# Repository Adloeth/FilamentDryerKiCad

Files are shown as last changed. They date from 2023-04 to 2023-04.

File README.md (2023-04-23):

# FilamentDryer KiCad

This is my first ever PCB design, nothing too interesting.

As this is my first electronic project with a custom PCB, this whole thing is a mess and I wouldn't do anything like this ever again ^^'

A lot of lessons were learned. I ordered and tested the board and everything is working as expected, but because I was ignorant there is a chance the whole PCB is a ticking bomb especially considering I totally forgot everything about it. Younger me might have miscalculated (or simply not calculated at all) some power usage somewhere, and it is possible a resistor, trace, component or whatever burst in flames and magic smokes.

## The Board

There aren't really that many components on this board, except a few resistors and MOSFETs. It mostly is a scaffolding for other PCBs : 
* Arduino Nano
* TCA9548A I²C multiplexer
* LM2596 buck converter to lower the voltage to 5V for the Arduino

The board has other peripherals :
* The DC 12V 5W 80°C PTC heating element
* AT24C256, an I²C EEPROM to store the temperature and humidity graphs.
* DHT22 sensor to control the heating element
* Two I²C OLED screens
* PC fan
* Loadcell and the HX711 (it's amplifier) to measure how many filament is left
* A few buttons to control everything

The Arduino code can be found on [another repository](https://github.com/Adloeth/FilamentDryer).

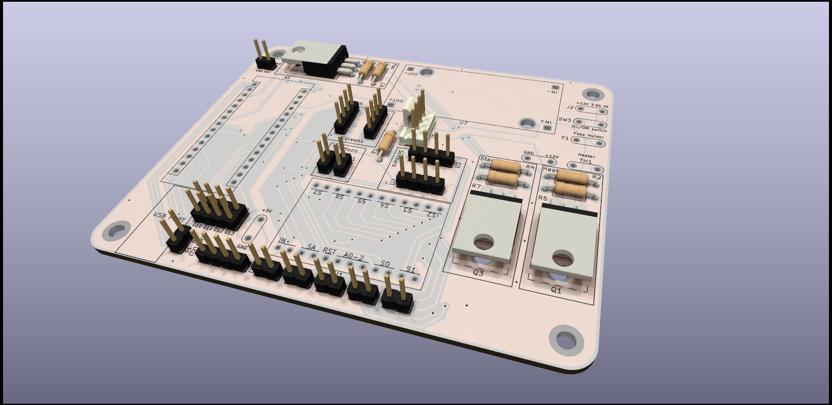
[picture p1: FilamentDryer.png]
Little rendering


## Why I did all this

My 3D printer had a moisture problem (Apparently PETG doesn't like humidity that much). The solution to this problem was to put the filament in the oven for a few hours, but I am not dumb enough to put a plastic that can have any number of toxic additives in the same oven I used to bake the food I eat.

Some companies sell filament dryers, the lowest of which was 60€ at the time. After looking around on the Internet I found a [series of videos](https://www.youtube.com/watch?v=IPKQCZ75Vwg&list=PLU5lZZLWyxXBlUrfcWFHtYylawElMm2N6) from [My Tech Fun](https://www.youtube.com/@MyTechFun) comparing several dryers, the ones at the lowest prices were surprisingly ineffective and required a lot of DIY to make them more efficient. While the most expansive were absolutely overkill.

So I decided to make everything myself, making sure my dryer was working where the other ones wouldn't and that some features only the priciest had were available to mine. The whole BOM was to be around 70€, which was good enough. It even had extruded polystyrene for thermal insulation !

Ultimately, putting my filament in an IKEA 10.6L 365+ with a layer of silica gel at the bottom solved the moisture issue and this project only served for me to learn how to make and order PCBs using KiCad and [JLCPCB](https://jlcpcb.com/), which is a very useful skill for my other future projects. Maybe one day I'll properly finish it, especially if I ever buy polyamide filaments.

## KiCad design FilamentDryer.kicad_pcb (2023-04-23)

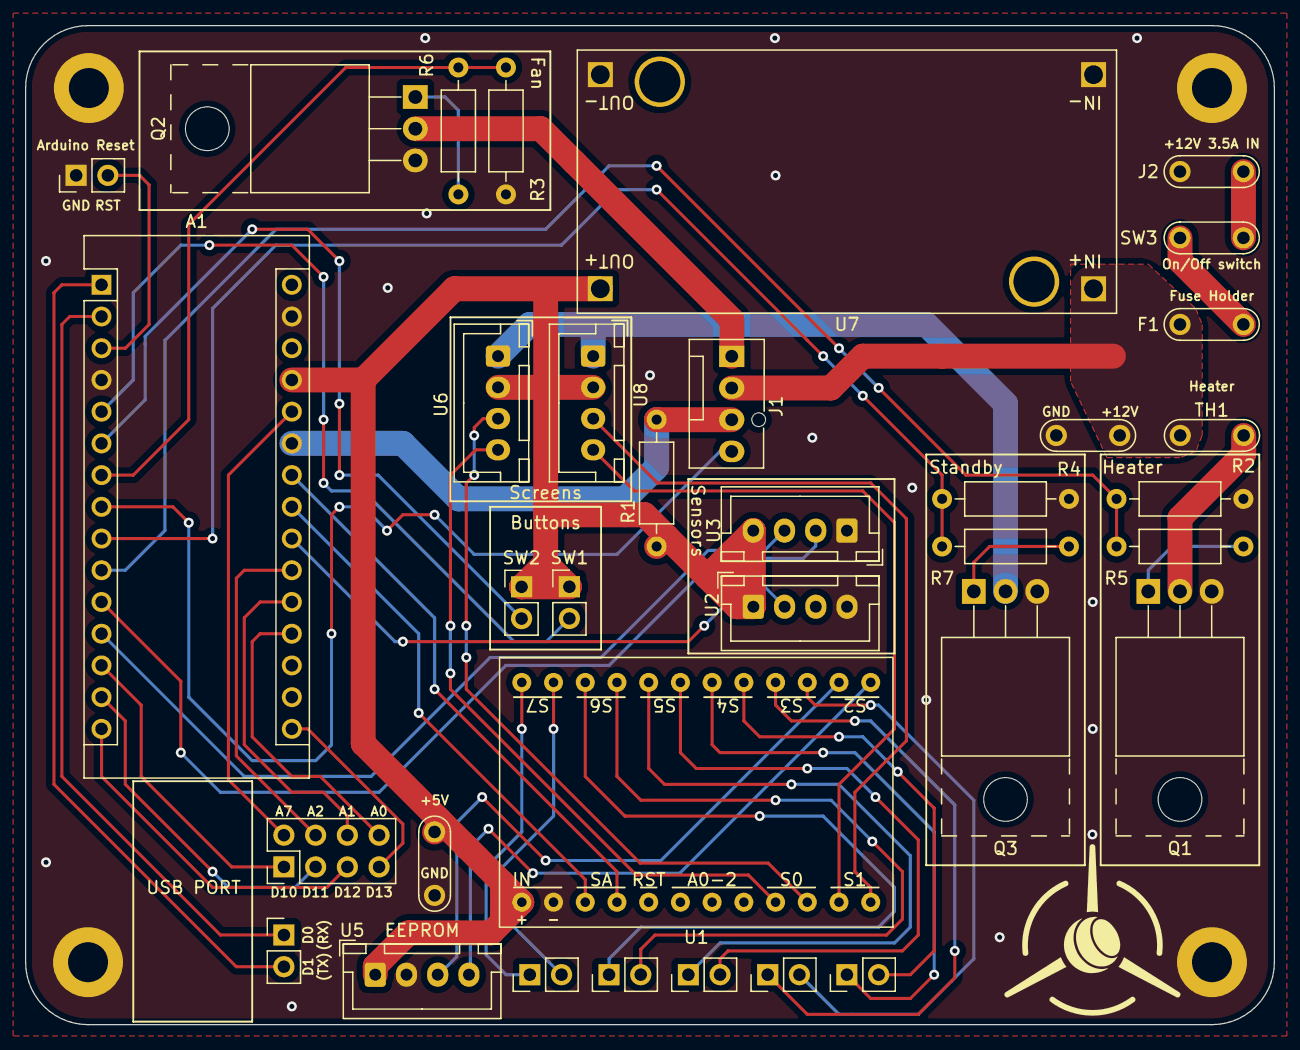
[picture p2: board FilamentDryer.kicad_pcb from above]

Board: 2 copper layers, 100.0 x 80.0 mm, 27 parts (0 on the bottom side), 29 nets.

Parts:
+5V_GND, +5V_GND#2: 7A_Connector_2Pin
A1: Arduino_Nano_v3.x; Arduino_Nano
F1: Fuse; 7A_Connector_2Pin
J1: Conn_01x04; FanPinHeader_1x04_P2.54mm_Vertical
J2: Barrel_Jack_Switch; 7A_Connector_2Pin
Q1, Q2, Q3: IRF540N; TO-220-3_Horizontal_TabUp
R1: 330; R_Axial_DIN0207_L6.3mm_D2.5mm_P10.16mm_Horizontal
R2, R3, R4: 10k; R_Axial_DIN0207_L6.3mm_D2.5mm_P10.16mm_Horizontal
R5, R6, R7: 220; R_Axial_DIN0207_L6.3mm_D2.5mm_P10.16mm_Horizontal
SW1, SW2: SW_Push; PinHeader_1x02_P2.54mm_Vertical
SW3: SW_SPST; 7A_Connector_2Pin
TH1: Thermistor_PTC; 7A_Connector_2Pin
U1: TCA9548A
U2: DHT22; JST_XH_B4B-XH-A_1x04_P2.50mm_Vertical
U3: HX711; JST_XH_B4B-XH-A_1x04_P2.50mm_Vertical
U5: AT24CXX; JST_XH_B4B-XH-A_1x04_P2.50mm_Vertical
U6, U8: OLED; JST_XH_B4B-XH-A_1x04_P2.50mm_Vertical
U7: LM2596S-ADJ-PCB; LM2596

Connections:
/ControlCircuit/+5V: +5V_GND#2.2, A1.27 (+5V), R1.1, SW1.1, SW2.1, U1.1 (VCC), U2.1 (VCC), U3.4 (VCC), U5.1 (VCC), U6.2 (VCC), U7.3 (OUT+), U8.2 (VCC)
/ControlCircuit/FanGND: J1.1, Q2.2 (D)
/ControlCircuit/FanPWM: A1.8 (D5), J1.4
/ControlCircuit/FanSwitch: A1.7 (D4), R3.1, R6.1
/ControlCircuit/FanTach: A1.25 (A6), J1.3, R1.2
/ControlCircuit/HeaterGND: Q1.2 (D), TH1.1
/ControlCircuit/HeaterSwitch: A1.10 (D7), R2.1, R5.1
/ControlCircuit/INT0: A1.5 (D2), SW1.2
/ControlCircuit/INT1: A1.6 (D3), SW2.2
/ControlCircuit/LCDAT: A1.11 (D8), U3.2 (DAT)
/ControlCircuit/LCSCK: A1.12 (D9), U3.3 (SCK)
/ControlCircuit/SBSwitch: A1.9 (D6), R4.1, R7.1
/ControlCircuit/SCL: A1.24 (A5), U1.4 (SCL)
/ControlCircuit/SDA: A1.23 (A4), U1.3 (SDA)
/ControlCircuit/U2A: A1.22 (A3), U2.2 (DAT)
/PowerSupply/+12V: +5V_GND.1, F1.2, J1.2, TH1.2, U7.1 (IN+)
GND: +5V_GND.2, +5V_GND#2.1, A1.4 (GND), A1.29 (GND), J2.2, Q1.3 (S), Q2.3 (S), Q3.3 (S), R2.2, R3.2, R4.2, U1.2 (GND), U2.4 (GND), U3.1 (GND), U5.2 (GND), U7.2 (IN-), U7.4 (OUT-)
GNDSB: Q3.2 (D), U6.1 (GND), U8.1 (GND)
unnamed: F1.1, SW3.2 (B)
unnamed: J2.1, SW3.1 (A)
unnamed: Q1.1 (G), R5.2
unnamed: Q2.1 (G), R6.2
unnamed: Q3.1 (G), R7.2
unnamed: U1.9 (SDA0), U6.4 (SDA)
unnamed: U1.10 (SCL0), U6.3 (SCL)
unnamed: U1.11 (SDA1), U8.4 (SDA)
unnamed: U1.12 (SCL1), U8.3 (SCL)
unnamed: U1.13 (SDA2), U5.4 (SDA)
unnamed: U1.14 (SCL2), U5.3 (SCL)
